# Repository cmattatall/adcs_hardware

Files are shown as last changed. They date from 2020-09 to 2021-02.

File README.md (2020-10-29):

# adcs_hardware
Hardware repository for ADCS

# Harware Architecture Overview

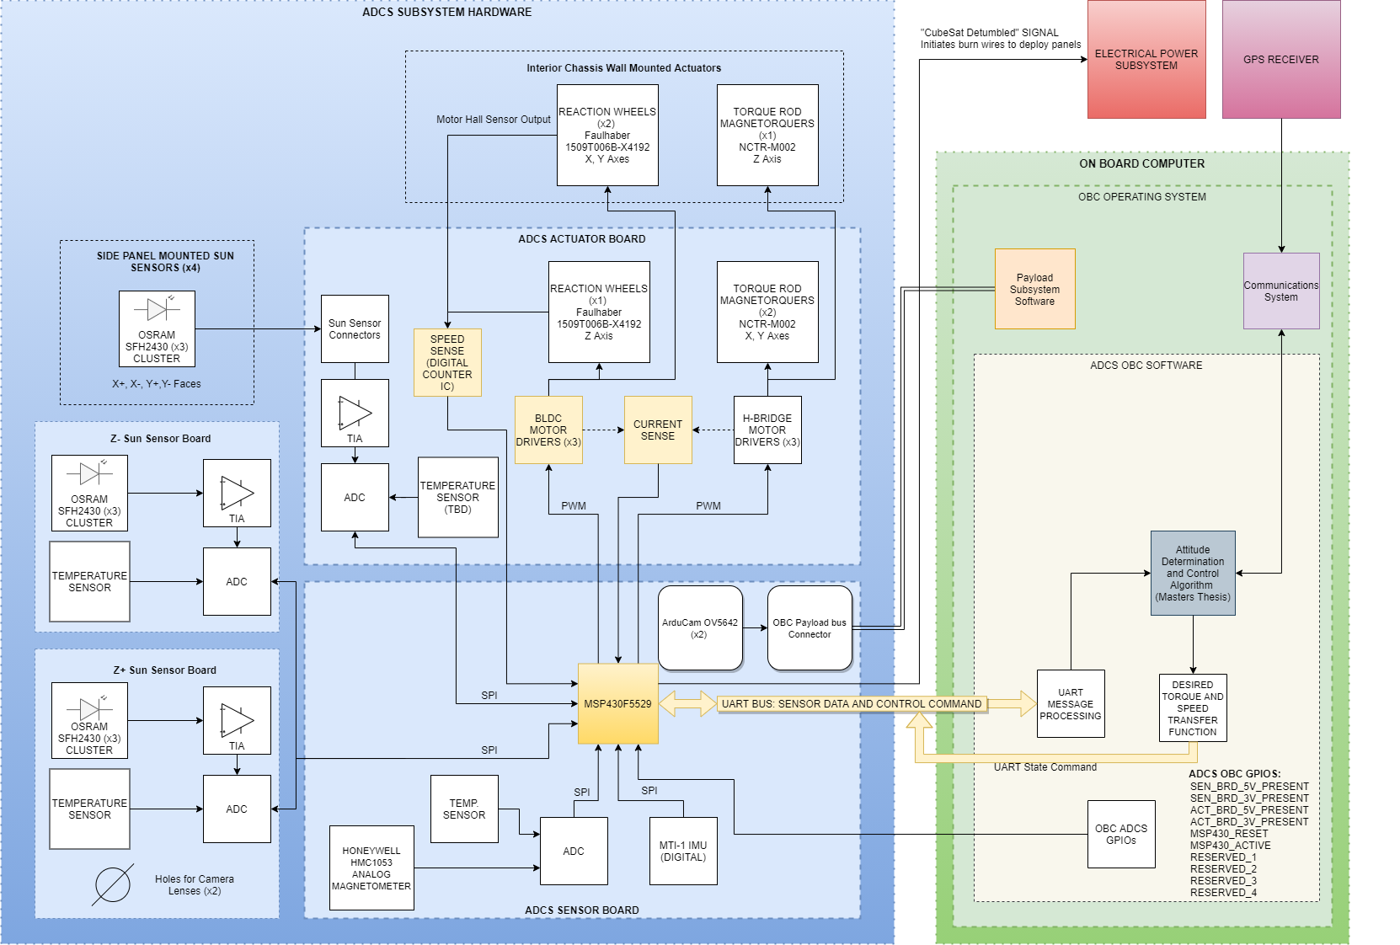
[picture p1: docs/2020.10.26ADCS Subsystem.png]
ADCS Hardware Block Diagram 2020.10.26


# VERSION CONTROL

WHENEVER A SHEMATIC REVISION IS COMPLETED, UNLIKE SOFTWARE, BRANCHES SHOULD NOT BE MERGED. THEY SHOULD BE FROZEN.

TO START A REVISION, THE CURRENT "HEAD" SHOULD BE FORKED (READ: MAKE A NEW BRANCH) NAMED APPROPRIATELY. 

If the revision is accepted and the design changes pass review, the revision branch then becomes the new master branch.

This way, the last "stable" revision branch (the old master branch) remains completely unchanged and unaffected by deltas made in the forked branch.

If there is ever an issue, the old version can be selected SIMPLY by switching back to the old branch, no merging should ever occur.

# Cloning repo for use in Eagle

Clone Repo into your local eagle projects repository
ie: C:/Users/user/Documents/Eagle/projects/

Repo will then appear under projects tab of the 'Control Panel' window when Eagle is launched.

# Eagle File Types Notes
 
## Project Manager File
*.epf is the eagle project manager file and contains all settings information for project. Contains all path references to all the libraries the have been used. *.epf is not crucial to project but can be useful to share with collaborators. 

## Design Files 
*.brd and *.sch files must have matching names and be contained in the same folder. Schematic files also copy all the information from the component libraries once the components are placed in a schematic, making the library files less necessary once used. The .brd files also copy the package information from the component libraries and don’t require libraries again unless you need to place a new component or replace a previous component. 

## Backup Files
*.b#x and *.s#x files are local backups by Eagle. By default Eagle saves 9 backups (9 is also the max).

## Libraries
Libraries are the templates for components. They are unique files that all the information on a specific component that Eagle CAD requires for design. They are the building blocks that contain information like pin numbers, terminal names, symbol shape, package type and footprint size etc. A library has both a symbol (used in schematics) and a package (footprint for pcb layout). Once a library is used in an Eagle design, it is no longer required as Eagle copies all the information over to the schematic and board files. However, while working with your team, it is recommended to share and use the same libraries to keep your designs consistent.

Custom library parts have been saved in managed library: https://library.io/libraries/22876504-my_library

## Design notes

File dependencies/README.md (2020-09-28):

# EDA DEPENDENCIES (EAGLE LIBS, DESIGN BLOCKS, CUSTOM FOOTPRINTS, AND OTHER DEPENDENCIES) GO HERE #

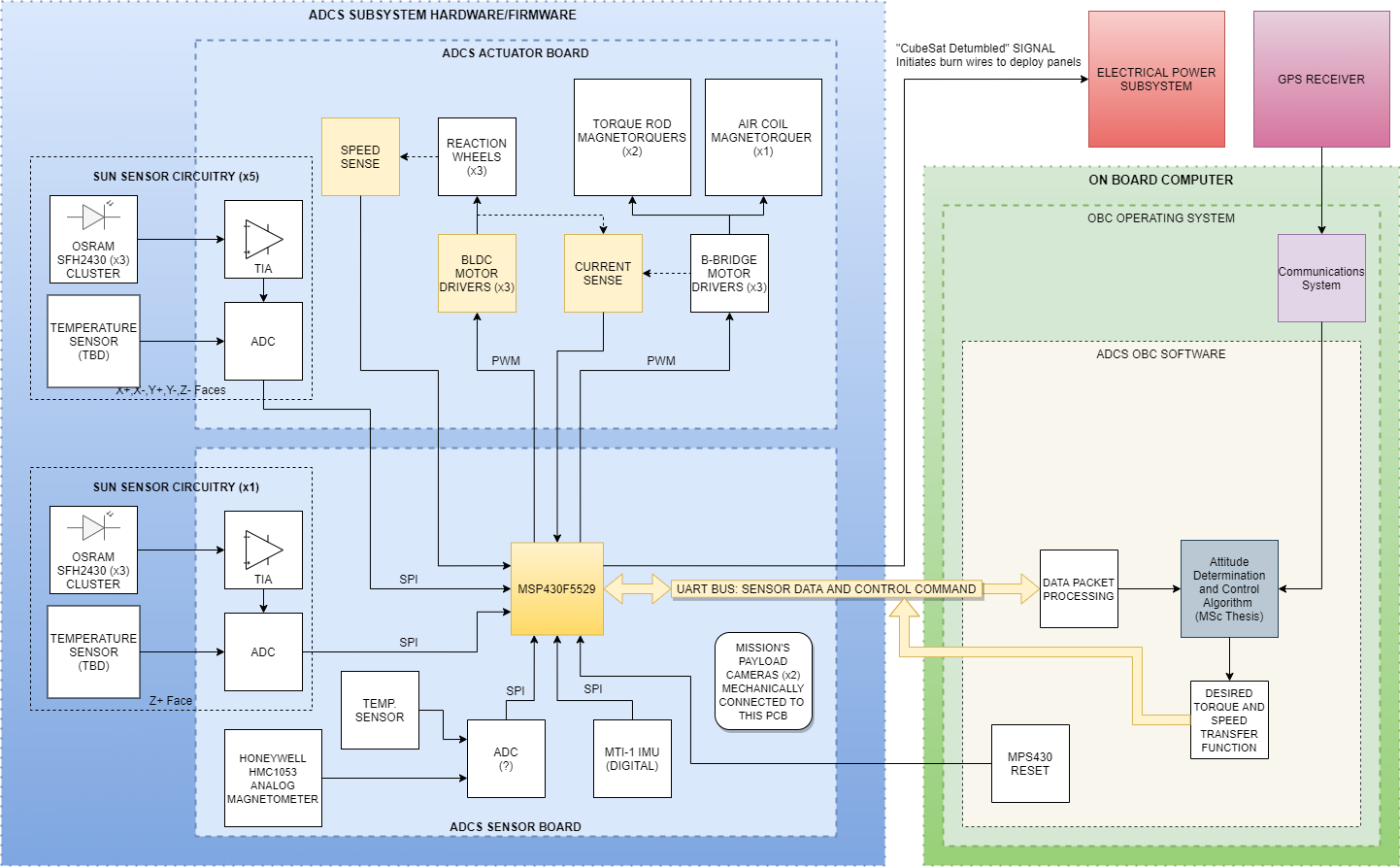
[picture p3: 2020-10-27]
docs/High Level Diagram 2020.09.08.png

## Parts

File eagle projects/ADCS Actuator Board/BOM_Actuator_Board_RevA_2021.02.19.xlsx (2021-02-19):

LORIS CubeSat Bill of Materials |  |  |  | Subsystem: ADCS
Dalhousie Space Systems Lab |  |  |  | PCB: Actuator Board | Rev: A |  | Date: 2021.02.19
Item | Qty | Manufacturer | MPN | Ref Des | Value | Footprint | Description | Digikey PN | Datasheet Link
1 | 12 | Yageo | AC0402KRX7R8BB223 | C54, C70, C71, C84, C98, C100, C101, C105, C110, C111, C115, C116 | 0.022u | C0402 | 0.022µF ±10% 25V Ceramic Capacitor X7R 0402 (1005 Metric) | 311-3068-1-ND | https://www.yageo.com/upload/media/product/productsearch/datasheet/mlcc/UPY-AC_NP0X7R_16V-to-630V_12.pdf
2 | 12 | Yageo | CC0603KRX7R8BB104 | C13, C16, C25, C26, C119, C121, C122, C126, C129, C130, C139, C142 | 0.1u | C0603 | 0.1µF ±10% 25V Ceramic Capacitor X7R 0603 (1608 Metric) | 311-1341-1-ND | https://www.yageo.com/upload/media/product/productsearch/datasheet/mlcc/UPY-GPHC_X7R_6.3V-to-50V_18.pdf
3 | 39 | Yageo | CS0402KRX7R8BB104 | C17, C21, C23, C27, C29, C37, C39, C43, C46, C48, C49, C51, C53, C56, C65, C67, C69, C73, C75, C76, C78, C79, C81, C83, C86, C88, C90, C92, C93, C95, C97, C102, C104, C107, C109, C112, C114, C123, C131 | 0.1u | C0402 | 0.1µF ±10% 25V Ceramic Capacitor X7R 0402 (1005 Metric) | 13-CS0402KRX7R8BB104CT-ND | https://www.yageo.com/upload/media/product/productsearch/datasheet/mlcc/UPY-ST_NPOX7R_16V-to-3KV_5.pdf
4 | 3 | Yageo | CC0603KRX7R8BB334 | C15, C125, C141 | 0.33u | C0603 | 0.33µF ±10% 25V Ceramic Capacitor X7R 0603 (1608 Metric) | 311-3573-1-ND | https://www.yageo.com/upload/media/product/productsearch/datasheet/mlcc/UPY-GPHC_X7R_6.3V-to-50V_18.pdf
5 | 3 | Yageo | CC0603KRX7R8BB474 | C64, C124, C132 | 0.47u | C0603 | 0.47µF ±10% 25V Ceramic Capacitor X7R 0603 (1608 Metric) | 311-1805-1-ND | https://www.yageo.com/upload/media/product/productsearch/datasheet/mlcc/UPY-GPHC_X7R_6.3V-to-50V_18.pdf
6 | 6 | TDK Corporation | CGA3E3X7R1H474M080AE | R19, R20, R48, R49, R83, R84 | 10K | R0603 | 0.47µF ±20% 50V Ceramic Capacitor X7R 0603 (1608 Metric) | 445-172476-1-ND | https://product.tdk.com/info/en/catalog/datasheets/mlcc_automotive_soft_en.pdf?ref_disty=digikey
7 | 9 | Yageo | RE0402FRE0710KL | R3, R4, R5, R6, R13, R14, R17, R30, R76 | 10k | R0402 | 10 kOhms ±1% 0.063W, 1/16W Chip Resistor 0402 (1005 Metric) Moisture Resistant Thick Film | 13-RE0402FRE0710KLCT-ND | https://www.yageo.com/upload/media/product/productsearch/datasheet/rchip/PYu-RE_105_RoHS_L_6.pdf
8 | 3 | Kemet | C0603C106M8PAC7411 | C42, C128, C144 | 10u | C0603 | 10µF ±20% 10V Ceramic Capacitor X5R 0603 (1608 Metric) | 399-C0603C106M8PAC7411CT-ND | https://api.kemet.com/component-edge/download/datasheet/C0603C106M8PAC7411.pdf
9 | 12 | Yageo | RC0402FR-0713K7L | R23, R28, R33, R39, R45, R51, R54, R57, R60, R63, R66, R69 | 13.7k | R0402 | 13.7 kOhms ±1% 0.063W, 1/16W Chip Resistor 0402 (1005 Metric) Moisture Resistant Thick Film | 311-13.7KLRCT-ND | https://www.yageo.com/upload/media/product/productsearch/datasheet/rchip/PYu-RC_Group_51_RoHS_L_11.pdf
10 | 3 | AVX Corporation | F981E105MMA | C14, C120, C140 | 1u | C0603 | 1µF Molded Tantalum Capacitors 25V 0603 (1608 Metric) 10Ohm | 478-8658-1-ND | http://datasheets.avx.com/F98.pdf
11 | 18 | Vishay Vitramon | VJ0402Y103KXJAC31 | C18, C22, C24, C28, C33, C40, C44, C45, C47, C50, C66, C72, C74, C77, C80, C89, C91, C94 | 1u | C0402 | 10000pF ±10% 16V Ceramic Capacitor X7R 0402 (1005 Metric) | 720-1250-1-ND | https://www.vishay.com/docs/45040/vj31vj34automlcc.pdf
12 | 3 | Kemet | C0603C225K4PACTU | C41, C127, C143 | 2.2u | C0603 | 2.2µF ±10% 16V Ceramic Capacitor X5R 0603 (1608 Metric) | 399-7886-1-ND | https://api.kemet.com/component-edge/download/datasheet/C0603C225K4PACTU.pdf
13 | 12 | Yageo | RC0402FR-07280RL | R22, R25, R32, R38, R44, R50, R53, R56, R59, R62, R65, R68 | 280R | R0402 | 280 Ohms ±1% 0.063W, 1/16W Chip Resistor 0402 (1005 Metric) Moisture Resistant Thick Film | 311-280LRCT-ND | https://www.yageo.com/upload/media/product/productsearch/datasheet/rchip/PYu-RC_Group_51_RoHS_L_11.pdf
14 | 6 | Yageo | RT0603FRE073K3L | R35, R36, R73, R74, R86, R87 | 3.3k | R0603 | 3.3 kOhms ±1% 0.1W, 1/10W Chip Resistor 0603 (1608 Metric) Thin Film | YAG3354CT-ND | https://www.yageo.com/upload/media/product/productsearch/datasheet/rchip/PYu-RT_1-to-0.01_RoHS_L_12.pdf
15 | 3 | Yageo | RC0402FR-0735KL | R18, R71, R77 | 35k | R0402 | 35 kOhms ±1% 0.063W, 1/16W Chip Resistor 0402 (1005 Metric) Moisture Resistant Thick Film | 13-RC0402FR-0735KLCT-ND | https://www.yageo.com/upload/media/product/productsearch/datasheet/rchip/PYu-RC_Group_51_RoHS_L_11.pdf
16 | 9 | Yageo | RC0402FR-074K7L | R1, R2, R7, R8, R9, R10, R11, R12, R15 | 4.7k | R0402 | 4.7 kOhms ±1% 0.063W, 1/16W Chip Resistor 0402 (1005 Metric) Moisture Resistant Thick Film | 311-4.7KLRCT-ND | https://www.yageo.com/upload/media/product/productsearch/datasheet/rchip/PYu-RC_Group_51_RoHS_L_11.pdf
17 | 12 | AVX Corporation | F981A475MMUAJ6 | C52, C55, C68, C82, C85, C87, C96, C99, C103, C106, C108, C113 | 4.7u | C0402 | 4.7µF Molded Tantalum Capacitors 10V 0603 (1608 Metric) 6Ohm @ 100kHz | 478-F981A475MMUAJ6CT-ND | http://datasheets.avx.com/F98.pdf
18 | 12 | Yageo | RC0402FR-073K74L | R24, R31, R34, R40, R46, R52, R55, R58, R61, R64, R67, R70 | 3.74k | R0402 | 3.74 kOhms ±1% 0.063W, 1/16W Chip Resistor 0402 (1005 Metric) Moisture Resistant Thick Film | 311-3.74KLRCT-ND | https://www.yageo.com/upload/media/product/productsearch/datasheet/rchip/PYu-RC_Group_51_RoHS_L_11.pdf
19 | 2 | Yageo | RC0603FR-07510RL | R26, R27 | 500R | R0603 | 510 Ohms ±1% 0.1W, 1/10W Chip Resistor 0603 (1608 Metric) Moisture Resistant Thick Film | 311-510HRCT-ND | https://www.yageo.com/upload/media/product/productsearch/datasheet/rchip/PYu-RC_Group_51_RoHS_L_11.pdf
20 | 3 | Yageo | RC0402FR-075R1L | R16, R29, R75 | 5R | R0402 | 5.1 Ohms ±1% 0.063W, 1/16W Chip Resistor 0402 (1005 Metric) Moisture Resistant Thick Film | YAG3370CT-ND | https://www.yageo.com/upload/media/product/productsearch/datasheet/rchip/PYu-RC_Group_51_RoHS_L_11.pdf
21 | 3 | Yageo | RT0603FRE0775KL | R21, R72, R85 | 75K | R0603 | 75 kOhms ±1% 0.1W, 1/10W Chip Resistor 0603 (1608 Metric) Thin Film | YAG5969CT-ND | https://www.yageo.com/upload/media/product/productsearch/datasheet/rchip/PYu-RT_1-to-0.01_RoHS_L_12.pdf
22 | 6 | Texas Instruments | ADS7841E/2K5 | U2, U3, U4, U13, U25, U27 | ADS7841E/2K5 |  | 12 Bit Analog to Digital Converter 4 Input 1 SAR 16-SSOP | 296-25900-1-ND | http://www.ti.com/lit/gpn/ADS7841
23 | 3 | Rohm Semiconductor | BD6210F-E2 | U9, U35, U39 | BD6210F-E2 | 8-SOP | Motor Driver Power MOSFET On/Off 8-SOP | BD6210F-E2CT-ND | http://rohmfs.rohm.com/en/products/databook/datasheet/ic/motor/dc/bd621x-e.pdf
24 | 15 | On Shore Technology Inc. | OSTVN02A150 | J7, J8, J9, J10, J11, J12, J13, J14, J15, J16, J17, J18, JX, JY, JZ | DNP | DO NOT POPULATE | TERM BLK 2P SIDE ENT 2.54MM PCB | ED10561-ND | http://www.on-shore.com/wp-content/uploads/OSTVNXXA150.pdf
25 | 3 | N/A | N/A | JP5, JP7, JP9 | DNP | DO NOT POPULATE | Pin Header Male 1x02 2.54MM | N/A | N/A
26 | 4 | N/A | N/A | J1, J4, J5, J6 | DNP | DO NOT POPULATE | Pin Header Male 1x03 2.54MM | N/A | N/A
27 | 2 | N/A | N/A | J2, J3 | DNP | DO NOT POPULATE | Pin Header Male 2x08 2.54MM | N/A | N/A
28 | 2 | N/A | N/A | MX, MY | DNP | DO NOT POPULATE | NCTR-M002 Torque Rod Assembly | N/A | N/A
29 | 1 | N/A | N/A | RWZ | DNP | DO NOT POPULATE | DSS LORIS Reaction Wheel Assembly | N/A | N/A
30 | 3 | Texas Instruments | DRV10970PWPR | U7, U10, U12 | DRV10970 | 24-HTSSOP | Motor Driver Power MOSFET PWM 24-HTSSOP | 296-44066-1-ND | http://www.ti.com/general/docs/suppproductinfo.tsp?distId=10
31 | 2 | Lite-On Inc. | LTST-C190GKT | LED1, LED2 | GREEN | LED0603 | Green 569nm LED Indication - Discrete 2.1V 0603 (1608 Metric) | 160-1183-1-ND | https://media.digikey.com/pdf/Data%20Sheets/Lite-On%20PDFs/LTST-C190GKT.pdf
32 | 3 | TE Connectivity AMP Connectors | 1-84953-1 | J19, J20, J21 | TE_1-84953-1 | SMD | 11 Position FPC Connector Contacts, Top 0.039" (1.00mm) Surface Mount, Right Angle | A101403CT-ND | https://www.te.com/commerce/DocumentDelivery/DDEController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
33 | 12 | Texas Instruments | TLV9051IDCKR | U6, U15, U19, U21, U23, U24, U26, U28, U29, U30, U31, U32 | TLV9051IDCKR | SC-70-5 | General Purpose Amplifier 1 Circuit Rail-to-Rail SC-70-5 | 296-TLV9051IDCKRCT-ND | http://www.ti.com/general/docs/suppproductinfo.tsp?distId=10
34 | 3 | STMicroelectronics | TSV991AILT | U1, U5, U8 | TSV991AILT | SOT-23-5 | General Purpose Amplifier 1 Circuit Rail-to-Rail SOT-23-5 | 497-5833-1-ND | http://www.st.com/content/ccc/resource/technical/document/datasheet/d8/e3/a5/aa/8f/d7/42/67/CD00144611.pdf/files/CD00144611.pdf/jcr:content/translations/en.CD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

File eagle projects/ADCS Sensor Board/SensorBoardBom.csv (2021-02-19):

Part | Value | Device | Package | Description
A1 | HMC1053PA0242 | HMC1053PA0242 | PA0242
A2 | ARDUCAM_OV5642 | ARDUCAM_OV5642 | ARDUCAM
A3 | ARDUCAM_OV5642 | ARDUCAM_OV5642 | ARDUCAM
C1 | 100n | C-EUC0402 | C0402 | CAPACITOR, European symbol
C2 | 10u | POLARIZED_CAP | A/3216-18R
C3 | 12p | C-EUC0402 | C0402 | CAPACITOR, European symbol
C4 | 12p | C-EUC0402 | C0402 | CAPACITOR, European symbol
C5 | 100n | C-EUC0402 | C0402 | CAPACITOR, European symbol
C6 | 470n | C-EUC0402 | C0402 | CAPACITOR, European symbol
C7 | 1n | C-EUC0402 | C0402 | CAPACITOR, European symbol
C8 | 100n | C-EUC0402 | C0402 | CAPACITOR, European symbol
C9 | 1u | C-EUC1206 | C1206 | CAPACITOR, European symbol
C10 | 0.1u | C-EUC0603 | C0603 | CAPACITOR, European symbol
C11 | 0.1u | C-EUC0603 | C0603 | CAPACITOR, European symbol
C12 | 1u | C-EUC1206 | C1206 | CAPACITOR, European symbol
C13 | 1u | C-EUC1206 | C1206 | CAPACITOR, European symbol
C14 | 0.1u | C-EUC0603 | C0603 | CAPACITOR, European symbol
C15 | 0.1u | C-EUC0603 | C0603 | CAPACITOR, European symbol
C16 | 0.1u | C-EUC0603 | C0603 | CAPACITOR, European symbol
C17 | 1n | C-EUC0805 | C0805 | CAPACITOR, European symbol
C18 | 1n | C-EUC1206 | C1206 | CAPACITOR, European symbol
C19 | 0.1u | C-EUC0603 | C0603 | CAPACITOR, European symbol
C20 | 0.1u | C-EUC0603 | C0603 | CAPACITOR, European symbol
C21 | 1n | C-EUC0805 | C0805 | CAPACITOR, European symbol
C22 | 0.1u | C-EUC0603 | C0603 | CAPACITOR, European symbol
C23 | 1n | C-EUC0805 | C0805 | CAPACITOR, European symbol
C24 | 470n | C-EUC0805 | C0805 | CAPACITOR, European symbol
J1 | HDR_10_EZFET_DEBUGGER | HDR_10_EZFET_DEBUGGER | HDRV10W66P254_10X1_2540X254H858
J2 | MTI-1_8428-11B1-RK-TP | MTI-1_8428-11B1-RK-TP | PLCC-28_SOCKET_TH
JP1 |  | PINHD-1X4 | 1X04 | PIN HEADER
JP2 |  | PINHD-2X8 | 2X08 | PIN HEADER
JP3 |  | PINHD-2X8 | 2X08 | PIN HEADER
JP4 |  | PINHD-1X4 | 1X04 | PIN HEADER
JP5 |  | PINHD-2X6 | 2X06 | PIN HEADER
JP6 |  | JP1Q_ | 1X02 | JUMPER
JP7 |  | PINHD-1X7 | 1X07 | PIN HEADER
JP8 |  | PINHD-1X4 | 1X04 | PIN HEADER
JP9 |  | PINHD-1X3 | 1X03 | PIN HEADER
LED1 |  | LEDCHIP-LED0603 | CHIP-LED0603 | LED
LED2 |  | LEDCHIP-LED0603 | CHIP-LED0603 | LED
LED3 |  | LEDCHIP-LED0603 | CHIP-LED0603 | LED
MH1 | MTGP700H400 | MTGP700H400 | MTGP700H400
MH2 | MTGP700H400 | MTGP700H400 | MTGP700H400
MH3 | MTGP700H400 | MTGP700H400 | MTGP700H400
MH4 | MTGP700H400 | MTGP700H400 | MTGP700H400
Q1 | BC850SMD | BC850SMD | SOT23-BEC | NPN Transistor
Q2 | IRF7507TRPBF | IRF7507TRPBF | SOP8P65_300X490X111L53X30N
R1 | 0R | R-US_R0402 | R0402 | RESISTOR, American symbol
R2 | 1k | R-US_R0402 | R0402 | RESISTOR, American symbol
R3 | 2k | R-US_R0402 | R0402 | RESISTOR, American symbol
R4 | 1k | R-US_R0402 | R0402 | RESISTOR, American symbol
R5 | 2k | R-US_R0402 | R0402 | RESISTOR, American symbol
R6 | 1M | R-US_R0402 | R0402 | RESISTOR, American symbol
R7 | 47k | R-US_R0402 | R0402 | RESISTOR, American symbol
R8 | 470R | R-US_R0603 | R0603 | RESISTOR, American symbol
R9 | 200R | R-US_R1206 | R1206 | RESISTOR, American symbol
R10 | 1k | R-US_R0805 | R0805 | RESISTOR, American symbol
R11 | 1k | R-US_R0805 | R0805 | RESISTOR, American symbol
R12 | 5.6k | R-US_R0805 | R0805 | RESISTOR, American symbol
R13 | 5.6k | R-US_R0805 | R0805 | RESISTOR, American symbol
R14 | 1.37M | R-US_R0805 | R0805 | RESISTOR, American symbol
R15 | 1.37M | R-US_R0805 | R0805 | RESISTOR, American symbol
R16 | 0R | R-US_R0805 | R0805 | RESISTOR, American symbol
R17 | 1k | R-US_R0805 | R0805 | RESISTOR, American symbol
R18 | 1k | R-US_R0805 | R0805 | RESISTOR, American symbol
R19 | 5.1M | R-US_R1206 | R1206 | RESISTOR, American symbol
R20 | 5.6k | R-US_R0805 | R0805 | RESISTOR, American symbol
R21 | 5.6k | R-US_R0805 | R0805 | RESISTOR, American symbol
R22 | 1.37M | R-US_R0805 | R0805 | RESISTOR, American symbol
R23 | 1.37M | R-US_R0805 | R0805 | RESISTOR, American symbol
R24 | 1k | R-US_R0805 | R0805 | RESISTOR, American symbol
R25 | 1k | R-US_R0805 | R0805 | RESISTOR, American symbol
R26 | 5.6k | R-US_R0805 | R0805 | RESISTOR, American symbol
R27 | 5.6k | R-US_R0805 | R0805 | RESISTOR, American symbol
R28 | 1.37M | R-US_R0805 | R0805 | RESISTOR, American symbol
R29 | 1.37M | R-US_R0805 | R0805 | RESISTOR, American symbol
R30 | 27R | R-US_R0805 | R0805 | RESISTOR, American symbol
R31 | 470R | R-US_R0603 | R0603 | RESISTOR, American symbol
R32 | 750R | R-US_R0603 | R0603 | RESISTOR, American symbol
R33 | 0R | R-US_R0805 | R0805 | RESISTOR, American symbol
R34 | 0R | R-US_R0805 | R0805 | RESISTOR, American symbol
R35 | 0R | R-US_R0805 | R0805 | RESISTOR, American symbol
S1 | RST | 10-XX | B3F-10XX | OMRON SWITCH
TP1 | TESTPOINT | TESTPOINT | TP_P76H50
TP2 | TESTPOINT | TESTPOINT | TP_P76H50
TP3 | TESTPOINT | TESTPOINT | TP_P76H50
TP4 | TESTPOINT | TESTPOINT | TP_P76H50
TP5 | TESTPOINT | TESTPOINT | TP_P76H50
U1 | MSP430F5529IPN | MSP430F5529IPN | QFP80P50_1400X1400X160L60X22N
U2 | LMV321 | LMV321 | SOT23-5P65_210X110L36X22N
U3 | ADS7841E_2K5 | ADS7841E_2K5 | DBQ16
U4 | LMV321 | LMV321 | SOT23-5P65_210X110L36X22N
U5 | LMV321 | LMV321 | SOT23-5P65_210X110L36X22N
Y1 | 32.768kHz | MS3V-T1R | MS3V-T1R
Y2 | CSTCR4M00G15L99 | CSTCR4M00G15L996M00G53Z | MURATA-FILTER_CSTCR

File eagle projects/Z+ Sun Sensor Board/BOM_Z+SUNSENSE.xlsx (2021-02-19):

LORIS ADCS |  |  |  | BILL OF MATERIALS
BOARD: Z+ SUN SENSE BOARD |  |  |  | REV A | Date: 2021.02.14
Item | Qty | MPN | Reference Designator | Value | Footprint | Description | Datasheet
1 | 1 | DO NOT POPULATE | A1 | DO NOT POPULATE | Custom | Sun Sensor Mount | -
2 | 3 | VJ0402Y103KXJAC31 | C14, C16, C21 | 1u | C0402 | CAP CER 10000PF 16V X7R 0402 | https://www.vishay.com/docs/45040/vj31vj34automlcc.pdf
3 | 8 | CS0402KRX7R8BB104 | C12, C15, C19, C20, C22, C26, C29, C31 | 0.1u | C0402 | CAP CER 0.1UF 25V X7R 0402 | https://www.yageo.com/upload/media/product/productsearch/datasheet/mlcc/UPY-ST_NPOX7R_16V-to-3KV_5.pdf
4 | 3 | CL21B475KOFNNNE | C25, C28, C30 | 4.7u | C0805 | CAP CER 4.7UF 16V X7R 0805 | https://media.digikey.com/pdf/Data%20Sheets/Samsung%20PDFs/CL_Series_MLCC_ds.pdf
5 | 3 | AC0402KRX7R8BB223 | C27, C32, C33 | 0.022u | C0402 | CAP CER 0.022UF 25V X7R 0402 | https://www.yageo.com/upload/media/product/productsearch/datasheet/mlcc/UPY-AC_NP0X7R_16V-to-630V_12.pdf
6 | 3 | DO NOT POPULATE | J4, J5, J6 | DO NOT POPULATE | DO NOT POPULATE | Terminal Block Connector 1x02 | -
7 | 1 | DO NOT POPULATE | JP3 | DO NOT POPULATE | DO NOT POPULATE | PIN HEADER | -
8 | 3 | RC0402FR-07280RL | R1, R8, R14 | 280R | R0402 | RES SMD 280 OHM 1% 1/16W 0402 | https://www.yageo.com/upload/media/product/productsearch/datasheet/rchip/PYu-RC_Group_51_RoHS_L_11.pdf
9 | 1 | RC0805JR-070RL | R2 | 0R | R0805 | RES SMD 0 OHM JUMPER 1/8W 0805 | https://www.yageo.com/upload/media/product/productsearch/datasheet/rchip/PYu-RC_Group_51_RoHS_L_11.pdf
10 | 1 | RE0402FRE0710KL | R20 | 10k | R0402 | RES SMD 10K OHM 1% 1/16W 0402 | https://www.yageo.com/upload/media/product/productsearch/datasheet/rchip/PYu-RE_105_RoHS_L_6.pdf
11 | 1 | RC0402JR-075M1L | R26 | 5.1M | R0402 | RES SMD 5.1M OHM 5% 1/16W 0402 | https://www.yageo.com/upload/media/product/productsearch/datasheet/rchip/PYu-RC_Group_51_RoHS_L_11.pdf
12 | 3 | RC0402FR-0713K7L | R3, R9, R15 | 13.7k | R0402 | RES SMD 13.7K OHM 1% 1/16W 0402 | https://www.yageo.com/upload/media/product/productsearch/datasheet/rchip/PYu-RC_Group_51_RoHS_L_11.pdf
13 | 3 | RC0402FR-073K74L | R7, R13, R19 | 5.6k | R0402 | RES SMD 3.74K OHM 1% 1/16W 0402 | https://www.yageo.com/upload/media/product/productsearch/datasheet/rchip/PYu-RC_Group_51_RoHS_L_11.pdf
14 | 1 | ADS7841E | U2 | ADS7841E_2K5 | DBQ16 | 12 Bit Analog to Digital Converter 4 Input 1 SAR 16-SSOP | http://www.ti.com/lit/gpn/ADS7841
15 | 1 | LM20BIM7X | U4 | LM20BIM7X_NOPB | SOT23-5P65_210X110L40X22N_LM20 | Temperature Sensor Analog, Local -55°C ~ 130°C 11.77mV/°C SC-70-5 | https://www.ti.com/lit/ds/symlink/lm20.pdf?ts=1611799060094
16 | 3 | TLV9051IDCKR | U6, U8, U9 | TLV9051IDCKR | SC70-5P65_210X110L36X22N_TLV9051 | General Purpose Amplifier 1 Circuit Rail-to-Rail SC-70-5 | https://www.ti.com/lit/ds/symlink/tlv9051.pdf?HQS=dis-dk-null-digikeymode-dsf-pf-null-wwe&ts=1611796011779

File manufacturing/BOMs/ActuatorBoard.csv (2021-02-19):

Item | QTY | MPN | REFDES | Value | Footprint | Description | Source | Link
1 | 3 | RE0402FRE0710KL | R37, R43, R49 | 10K | 402 | Metal film resistor | Digikey | https://www.digikey.ca/en/products/detail/yageo/RE0402FRE0710KL/5922980
2 | 3 | RC0402FR-0735KL | R36, R42, R48 | 35K | 402 | Metal film resistor | Digikey | https://www.digikey.ca/en/products/detail/yageo/RC0402FR-0735KL/5917655
3 | 38 | CC0603JPX7R9BB104 | C2, C7, C9, C10, C12, C13, C14, C15, C16, C17, C18, C19, C21, C22, C23, C24, C25, C26, C27, C28, C31, C35, C40, C44, C46, C51, C53, C54, C57, C59, C68, C73, C75, C76, C90, C95, C97, C98 | 100n | 603 | X7R Ceramic Capacitor | Digikey | https://www.digikey.ca/en/products/detail/yageo/CC0603JPX7R9BB104/11490924
4 | 3 | C1608X7R1H334M080AC | C30, C34, C38 | 330n | 603 | X7R Ceramic Capacitor | Digikey | https://www.digikey.ca/en/products/detail/tdk-corporation/C1608X7R1H334M080AC/2443429
5 | 3 | CGA3E3X7R1H474M080AE | C39, C41, C42, C61 | 470n | 603 | X7R Ceramic Capacitor | Digikey | https://www.digikey.ca/en/products/detail/tdk-corporation/CGA3E3X7R1H474M080AE/4989851
6 | 42 | CGA3E3X7R1H474M080AE | R1,R2, R3, R4, R5, R6, R7, R8, R9, R10, R11, R12, R29, R30, R31, R32, R33, R38, R44, R60, R61, R85, R86, R87, R88, R89, R92, R93, R100, R101, R102, R103, R104, R105, R106, R107, R108, R109, R110, R111, R125, R126, | 10K | 603 | Metal film resistor | Digikey | https://www.digikey.ca/en/products/detail/yageo/RT0603FRD0710KL/5928954
7 | 3 |  | C29, C33, C37 | 10u | 603
8 | 24 | RC0603FR-0713K7L | R14, R15, R16, R17, R18, R19, R114, R115, R116, R117, R118, R119, R164, R165, R166, R167, R168, R169, R214, R215, R216, R217, R218, R219 | 13.7K | 603 | Metal film resistor | Digikey | https://www.digikey.ca/en/products/detail/yageo/RC0603FR-0713K7L/726933
9 | 19 | UMK107AB7105KA-T | C6, C8, C11, C20, C32, C36, C43, C50, C52, C55, C56, C58, C60, C72, C74, C77, C94, C96, C99 | 1u | 603 | X7R Ceramic Capacitor | Digikey | https://www.digikey.ca/en/products/detail/taiyo-yuden/UMK107AB7105KA-T/3660085
10 | 6 | RT0603FRE073K3L | R124, R127, R129, R130, R132, R133 | 3.3K | 603 | Metal film resistor | Digikey | https://www.digikey.ca/en/products/detail/yageo/RT0603FRE073K3L/1075348
11 | 4 |  | C1, C45, C67, C89 | 4.7u | 603
12 | 19 | RC0603FR-075M1L | R20, R21, R24, R25, R34, R39, R40, R45, R46, R53, R54, R55, R59, R120, R121, R170, R171, R220, R221 | 5.1M | 603 | Metal film resistor | Digikey | https://www.digikey.ca/en/products/detail/yageo/RC0603FR-075M1L/5918378
13 | 3 | RC0402FR-075R1L | R35, R41, R47 | 5R | 402 | Metal film resistor | Digikey | https://www.digikey.ca/en/products/detail/yageo/RC0402FR-075R1L/5917722
14 | 3 | RT0603FRE0775KL | R112, R128, R131 | 75K | 603 | Metal film resistor | Digikey | https://www.digikey.ca/en/products/detail/yageo/RT0603FRE0775KL/1075486
15 | 6 | ADS7841E/2K5 | U1, U9, U12, U13, U19, U25 | N/A | DBQ16 | 12Bit ADC : SPI Interface | Digikey | https://www.digikey.com/en/products/detail/texas-instruments/ADS7841E-2K5/300663
16 | 3 | BD6210F-E2 | U4, U5, U6 | N/A | SOP8 | H-bridge IC | Digikey | https://www.digikey.ca/en/products/detail/rohm-semiconductor/BD6210F-E2/1936313
17 | 19 | BSS138 | Q2, Q3, Q4, Q5, Q6, Q7, Q8, Q9, Q10, Q11, Q12, Q13, Q14, Q15, Q16, Q17, Q18, Q19, Q21 | N/A | SOT233 | N channel Discrete enhancement mode MOSFET | Digikey | https://www.digikey.com/en/products/detail/on-semiconductor/BSS138/244210
18 | 1 | CD4514BM96 | U14 | N/A | 24-SOIC | 4-bit latched line decoder | Digikey | https://www.digikey.ca/en/products/detail/texas-instruments/CD4514BM96/1691558
19 | 3 | DRV10970PWPR | U17, U18, U20 | N/A | 24-HTSSOP | 3-phase brushless DC motor driver IC | Digikey | https://www.digikey.ca/en/products/detail/texas-instruments/DRV10970PWPR/5985442
23 | 1 | REF194GSZ-REEL7 | U2 | N/A | 8-SOIC | Series voltage reference IC | Digikey | https://www.digikey.ca/en/products/detail/analog-devices-inc/REF194GSZ-REEL7/995868
24 | 12 | SFH 2430-Z | D4, D5, D6, D13, D14, D15, D19, D20, D21, D25, D26, D27 | N/A | 2-SMD, Gull Wing | Optoisolator | Digikey | https://www.digikey.ca/en/products/detail/osram-opto-semiconductors-inc/SFH-2430-Z/1668853
25 | 3 | SN74HC165DB | U8, U11, U16 | N/A | SOP16 | 8 bit parallel shift register | AliExpress | https://www.aliexpress.com/item/4000854321406.html
26 | 3 | SN74HC590AD | U7, U10, U14 | N/A | 16-SOIC | 8 bit binary counter | Digikey | https://www.digikey.com/en/products/detail/texas-instruments/SN74HC590AD/376756
27 | 4 | TLV9054IDR | U3, U15, U21, U27 | N/A | 14-SOIC | single rail CMOS OP-AMP | Digikey | https://www.digikey.com/en/products/detail/texas-instruments/TLV9054IDR/10273198
28 | 3 | TSV991AILT | U7, U8, U10 | N/A | SOT-23-5 | dual rail CMOS OP-AMP 20Mhz | Mouser | https://www.mouser.com/ProductDetail/STMicroelectronics/TSV991AILT/?qs=NCG0bTVqH4ejiP6AM1B8jw==
29 | 3 | Do not populate | JP1, JP2, JP3 | N/A | Do not populate | 0.1’ pitch male 1x2 rectangular pin header | Do not populate | Do not populate
30 | 1 | Do not populate | JP5 | N/A | Do not populate | Solder jumper | Do not populate | Do not populate
31 | 12 | Do not populate | TP1, TP2, TP3, TP4, TP5, TP6, TP7, TP8, TP9, TP10, TP11, TP12 | N/A | Do not populate | 0.1’ pitch male 1x1 rectangular pin header | Do not populate | Do not populate
32 | 3 | Do not populate | MX, MY, MZ | NCTR-M002_MOUNT | Do not populate | MQTR MOUNTING FRAME | Do not populate | Do not populate
33 | 3 | Do not populate | A1, A2, A3 | REACTION_WHEELASSEMBLY | Do not populate | RW MOUNTING FRAME | Do not populate | Do not populate

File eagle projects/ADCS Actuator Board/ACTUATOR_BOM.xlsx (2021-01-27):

LORIS ADCS ACTUATOR BOARD BILL OF MATERIALS (REVISION A)
Item | Qty | MPN | Reference Designator | Value | Footprint | Description | Source | Link
1 | 3 | RC0402FR-075R1L | R35, R41, R47 | 5R | 402 | Thick film resistor | Digikey | https://www.digikey.ca/en/products/detail/yageo/RC0402FR-075R1L/5917722
2 | 12 | RC0402FR-07280RL | R22, R25, R32, R38, R44, R50, R53, R56, R59, R62, R65, R68 | 280R | 402 | Thick film resistor | Digikey | https://www.digikey.ca/en/products/detail/yageo/RC0402FR-07280RL/726578
3 | 12 | RT0402BRD073K74L | R24, R31, R34, R40, R46, R52, R55, R58, R61, R64, R67, R70 | 3.74K | 402 | Thick film resistor | Digikey | https://www.digikey.ca/en/products/detail/yageo/RT0402BRD073K74L/1069258
4 | 9 | RE0402FRE0710KL | R13, R3, R4, R5, R6, R7, R36, R42, R48 | 10K | 402 | Thick film resistor | Digikey | https://www.digikey.ca/en/products/detail/yageo/RE0402FRE0710KL/5922980
5 | 12 | RC0402FR-0713K7L | R23, R28, R33, R39, R45, R51, R54, R57, R60, R63, R66, R69 | 13.7K | 402 | Thick film resistor | Digikey | https://www.digikey.ca/en/products/detail/yageo/RC0402FR-0713K7L/2827638
6 | 3 | RC0402FR-0735KL | R37, R43, R49 | 35K | 402 | Thick film resistor | Digikey | https://www.digikey.ca/en/products/detail/yageo/RC0402FR-0735KL/5917655
7 | 2 | RC0603FR-07510RL | R26, R27 | 500R | 603 | Thick film resistor | Digikey | https://www.digikey.ca/en/products/detail/yageo/RC0603FR-07510RL/727285
8 | 6 | RT0603FRE073K3L | R124, R127, R129, R130, R132, R133 | 3.3K | 603 | Thick film resistor | Digikey | https://www.digikey.ca/en/products/detail/yageo/RT0603FRE073K3L/1075348
9 | 7 | CGA3E3X7R1H474M080AE | R2, R8, R9, R10, R11, R100, R101 | 10K | 603 | Thick film resistor | Digikey | https://www.digikey.ca/en/products/detail/yageo/RT0603FRD0710KL/5928954
10 | 1 | RC0603FR-0724KL | R1 | 24K | 603 | Thick film resistor | Digikey | https://www.digikey.ca/en/products/detail/yageo/RC0603FR-0724KL/727076
11 | 3 | RT0603FRE0775KL | R112, R128, R131 | 75K | 603 | Thick film resistor | Digikey | https://www.digikey.ca/en/products/detail/yageo/RT0603FRE0775KL/1075486
12 | 12 | AC0402KRX7R8BB223 | C54, C70, C71, C84, C98, C100, C101, C105, C110, C111, C115, C116 | 0.022u | 402 | Ceramic SMD MLCC Capacitor | Digikey | https://www.digikey.ca/en/products/detail/yageo/AC0402KRX7R8BB223/6643054
13 | 28 | CS0402KRX7R8BB104 | C46, C48, C49, C51, C53, C65, C67, C69, C73, C75, C76, C78, C79, C81, C83, C86, C88, C90, C92, C93, C95, C97, C102, C104, C107, C109, C112, C114 | 0.1u | 402 | Ceramic SMD MLCC Capacitor | Digikey | https://www.digikey.ca/en/products/detail/yageo/CS0402KRX7R8BB104/6097896
14 | 12 | VJ0402Y103KXJAC31 | C28, C45, C47, C50, C66, C72, C74, C77, C80, C89, C91, C94 | 1u | 402 | Ceramic SMD MLCC Capacitor | Digikey | https://www.digikey.ca/en/products/detail/vishay-vitramon/VJ0402Y103KXJAC31/2972205
15 | 18 | F981A475MMUAJ6 | C2, C3, C4, C5, C6, C7, C52, C55, C68, C82, C85, C87, C96, C99, C103, C106, C108, C113 | 4.7u | 402 | SMD Molded Tantalum Capacitor | Digikey | https://www.digikey.ca/en/products/detail/avx-corporation/F981A475MMUAJ6/12321753
16 | 21 | CC0603KRX7R8BB104 | C1, C12, C13, C14, C15, C16, C17, C18, C19, C21, C23, C31, C35, C40, C44, C57, C59, C61, C62, C63, C64 | 0.1u | 603 | Ceramic SMD MLCC Capacitor | Digikey | https://www.digikey.ca/en/products/detail/yageo/CC0603KRX7R8BB104/2103079
17 | 3 | CC0603KRX7R8BB334 | C30, C34, C38 | 0.33u | 603 | Ceramic SMD MLCC Capacitor | Digikey | https://www.digikey.ca/en/products/detail/yageo/CC0603KRX7R8BB334/5883785
18 | 3 | CC0603KRX7R8BB474 | C39, C41, C42 | 0.47u | 603 | Ceramic SMD MLCC Capacitor | Digikey | https://www.digikey.ca/en/products/detail/yageo/CC0603KRX7R8BB474/5195213
19 | 7 | F981E105MMA | C20, C32, C36, C43, C56, C58, C60 | 1u | 603 | SMD Molded Tantalum Capacitor | Digikey | https://www.digikey.ca/en/products/detail/avx-corporation/F981E105MMA/4005086
20 | 1 | PLEASE QUOTE | LED1 | RED | 603 | Mono color Chip LED | FABRICATOR PROVIDED
21 | 1 | PLEASE QUOTE | LED2 | ORANGE | 603 | Mono color Chip LED | FABRICATOR PROVIDED
22 | 6 | ADS7841E/2K5 | U4, U9, U12, U13, U25, U27 | N/A | DBQ16 | 12Bit ADC : SPI Interface | Digikey | https://www.digikey.com/en/products/detail/texas-instruments/ADS7841E-2K5/300663
23 | 3 | BD6210F-E2 | U11, U16, U22 | N/A | SOP8 | H-bridge IC | Digikey | https://www.digikey.ca/en/products/detail/rohm-semiconductor/BD6210F-E2/1936313
24 | 3 | DRV10970PWPR | U17, U18, U20 | N/A | 24-HTSSOP | 3-phase brushless DC motor driver IC | Digikey | https://www.digikey.ca/en/products/detail/texas-instruments/DRV10970PWPR/5985442
25 | 12 | SFH 2430-Z | D1, D3, D5, D7, D8, D9, D10, D11, D12, D13, D14, D15 | N/A | 2-SMD, Gull Wing | Optoisolator | Digikey | https://www.digikey.ca/en/products/detail/osram-opto-semiconductors-inc/SFH-2430-Z/1668853
26 | 12 | TLV9051IDCKR | U6, U15, U19, U21, U23, U24, U26, U28, U29, U30, U31, U32 | N/A | 14-SOIC | single rail CMOS OP-AMP | Digikey | https://www.digikey.ca/en/products/detail/texas-instruments/TLV9051IDCKR/10715332
27 | 3 | TSV991AILT | U7, U8, U10 | N/A | SOT-23-5 | dual rail CMOS OP-AMP 20Mhz | Mouser | https://www.mouser.com/ProductDetail/STMicroelectronics/TSV991AILT/?qs=NCG0bTVqH4ejiP6AM1B8jw==
28 | 3 | DO NOT POPULATE | JP1, JP2, JP3 | DO NOT POPULATE |  | DO NOT POPULATE
29 | 1 | DO NOT POPULATE | J1 | DO NOT POPULATE |  | DO NOT POPULATE
30 | 2 | DO NOT POPULATE | J2, J3 | DO NOT POPULATE |  | DO NOT POPULATE
31 | 3 | DO NOT POPULATE | JX, JY, JZ | DO NOT POPULATE |  | DO NOT POPULATE
32 | 3 | DO NOT POPULATE | J4, J5, J6 | DO NOT POPULATE |  | DO NOT POPULATE

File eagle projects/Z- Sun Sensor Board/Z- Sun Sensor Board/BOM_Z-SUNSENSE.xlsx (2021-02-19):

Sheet: ZMinusSunSensorBoard
LORIS ADCS |  |  |  | BILL OF MATERIALS
BOARD: Z- SUN SENSE BOARD |  |  |  | REVISION: A | Date: 2021.01.28
Item | Qty | MPN | Reference Designator | Value | Footprint | Description | Package | Datasheet
1 | 1 | DO NOT POPULATE | A1 | DO NOT POPULATE | Custom | Sun Sensor Mount | SUN_SENOR_MASK | -
2 | 3 | VJ0402Y103KXJAC31 | C14, C16, C21 | 1u | 0402 | CAP CER 10000PF 16V X7R 0402 | C0402 | https://www.vishay.com/docs/45040/vj31vj34automlcc.pdf
3 | 8 | CS0402KRX7R8BB104 | C12, C15, C19, C20, C22, C26, C29, C31 | 0.1u | 0402 | CAP CER 0.1UF 25V X7R 0402 | C0402 | https://www.yageo.com/upload/media/product/productsearch/datasheet/mlcc/UPY-ST_NPOX7R_16V-to-3KV_5.pdf
4 | 3 | CL21B475KOFNNNE | C25, C28, C30 | 4.7u | 0805 | CAP CER 4.7UF 16V X7R 0805 | C0805 | https://media.digikey.com/pdf/Data%20Sheets/Samsung%20PDFs/CL_Series_MLCC_ds.pdf
5 | 3 | AC0402KRX7R8BB223 | C27, C32, C33 | 0.022u | 0402 | CAP CER 0.022UF 25V X7R 0402 | C0402 | https://www.yageo.com/upload/media/product/productsearch/datasheet/mlcc/UPY-AC_NP0X7R_16V-to-630V_12.pdf
6 | 3 | DO NOT POPULATE | J4, J5, J6 | DO NOT POPULATE | DO NOT POPULATE | Terminal Block Connector 1x02 | 2POL254 | -
7 | 1 | DO NOT POPULATE | JP3 | DO NOT POPULATE | DO NOT POPULATE | PIN HEADER | 1X06 | -
8 | 3 | RC0402FR-07280RL | R1, R8, R14 | 280R | 0402 | RES SMD 280 OHM 1% 1/16W 0402 | R0402 | https://www.yageo.com/upload/media/product/productsearch/datasheet/rchip/PYu-RC_Group_51_RoHS_L_11.pdf
9 | 1 | RC0805JR-070RL | R2 | 0R | 0805 | RES SMD 0 OHM JUMPER 1/8W 0805 | R0805 | https://www.yageo.com/upload/media/product/productsearch/datasheet/rchip/PYu-RC_Group_51_RoHS_L_11.pdf
10 | 1 | RE0402FRE0710KL | R20 | 10k | 0402 | RES SMD 10K OHM 1% 1/16W 0402 | R0402 | https://www.yageo.com/upload/media/product/productsearch/datasheet/rchip/PYu-RE_105_RoHS_L_6.pdf
11 | 1 | RC0402JR-075M1L | R26 | 5.1M | 0402 | RES SMD 5.1M OHM 5% 1/16W 0402 | R0603 | https://www.yageo.com/upload/media/product/productsearch/datasheet/rchip/PYu-RC_Group_51_RoHS_L_11.pdf
12 | 3 | RC0402FR-0713K7L | R3, R9, R15 | 13.7k | 0402 | RES SMD 13.7K OHM 1% 1/16W 0402 | R0402 | https://www.yageo.com/upload/media/product/productsearch/datasheet/rchip/PYu-RC_Group_51_RoHS_L_11.pdf
13 | 3 | RC0402FR-073K74L | R7, R13, R19 | 3.74k | 0402 | RES SMD 3.74K OHM 1% 1/16W 0402 | R0402 | https://www.yageo.com/upload/media/product/productsearch/datasheet/rchip/PYu-RC_Group_51_RoHS_L_11.pdf
14 | 1 | ADS7841E | U2 | ADS7841E_2K5 | 16-SSOP | 12 Bit Analog to Digital Converter 4 Input 1 SAR 16-SSOP | DBQ16 | http://www.ti.com/lit/gpn/ADS7841
15 | 1 | LM20BIM7X | U4 | LM20BIM7X_NOPB | SC-70-5 | Temperature Sensor Analog, Local -55°C ~ 130°C 11.77mV/°C SC-70-5 | SOT23-5P65_210X110L40X22N_LM20 | https://www.ti.com/lit/ds/symlink/lm20.pdf?ts=1611799060094
16 | 3 | TLV9051IDCKR | U6, U8, U9 | TLV9051IDCKR | SC-70-5 | General Purpose Amplifier 1 Circuit Rail-to-Rail SC-70-5 | SC70-5P65_210X110L36X22N_TLV9051 | https://www.ti.com/lit/ds/symlink/tlv9051.pdf?HQS=dis-dk-null-digikeymode-dsf-pf-null-wwe&ts=1611796011779

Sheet: BOM_ZMinusSunSensorBoard
LORIS ADCS Z- SUN SENSOR BOARD BILL OF MATERIALS (REVISION A)

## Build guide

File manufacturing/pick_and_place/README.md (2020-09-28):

# PICK AND PLACE FILES GO IN THIS FOLDER #

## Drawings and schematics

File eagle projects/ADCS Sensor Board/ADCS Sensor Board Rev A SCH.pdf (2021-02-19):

## Analog VCC

A

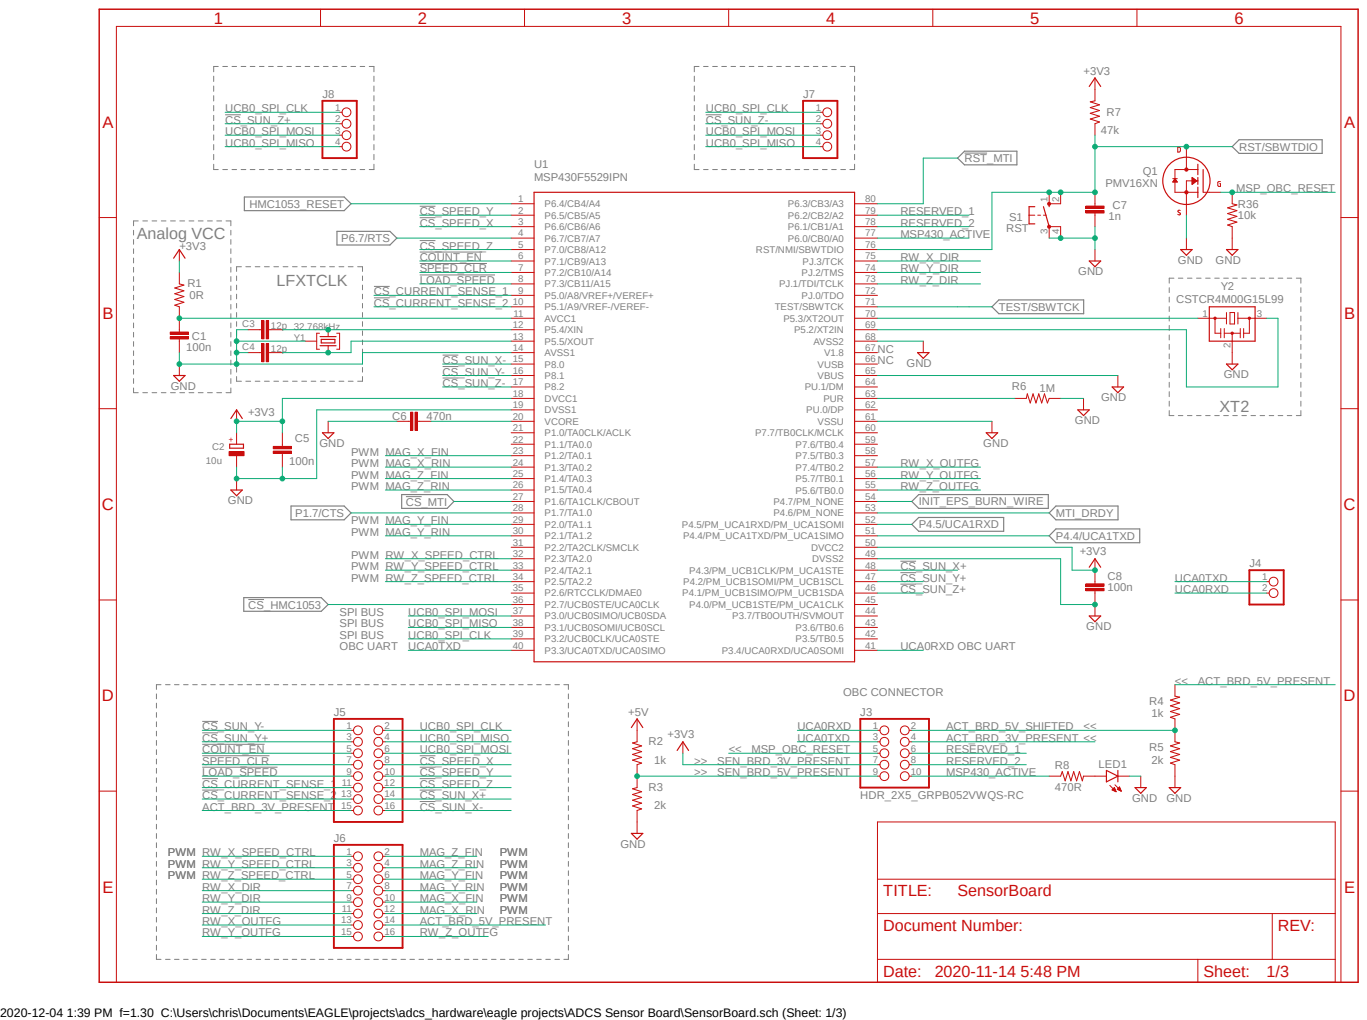
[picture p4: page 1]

C3 | 12p 32.768kHz | P5.4/XIN 12

Y1 | | | P5.5/XOUT 13

Document Number: | REV:

Date: 2020-11-14 5:48 PM | Sheet: 1/3

2020-12-04 1:39 PM f=1.30 C:\Users\chris\Documents\EAGLE\projects\adcs_hardware\eagle projects\ADCS Sensor Board\SensorBoard.sch (Sheet: 1/3)

A

A

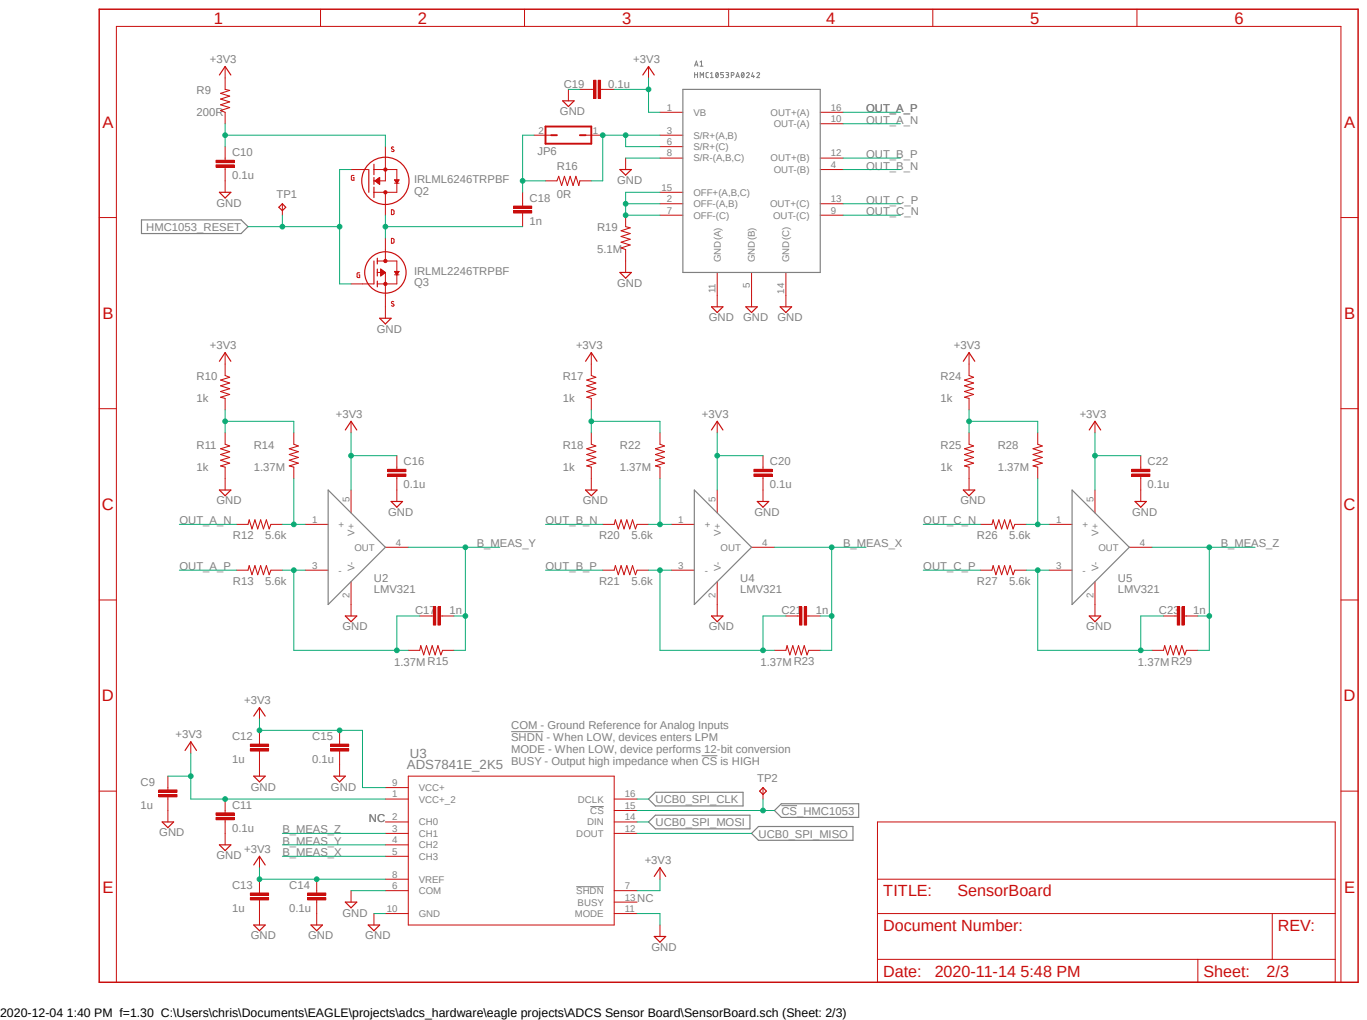
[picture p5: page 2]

COM - Ground Reference for Analog Inputs
SHDN - When LOW, devices enters LPM
MODE - When LOW, device performs 12-bit conversion
BUSY - Output high impedance when CS is HIGH

Document Number: | REV:

2020-12-04 1:40 PM f=1.30 C:\Users\chris\Documents\EAGLE\projects\adcs_hardware\eagle projects\ADCS Sensor Board\SensorBoard.sch (Sheet: 2/3)

A

A

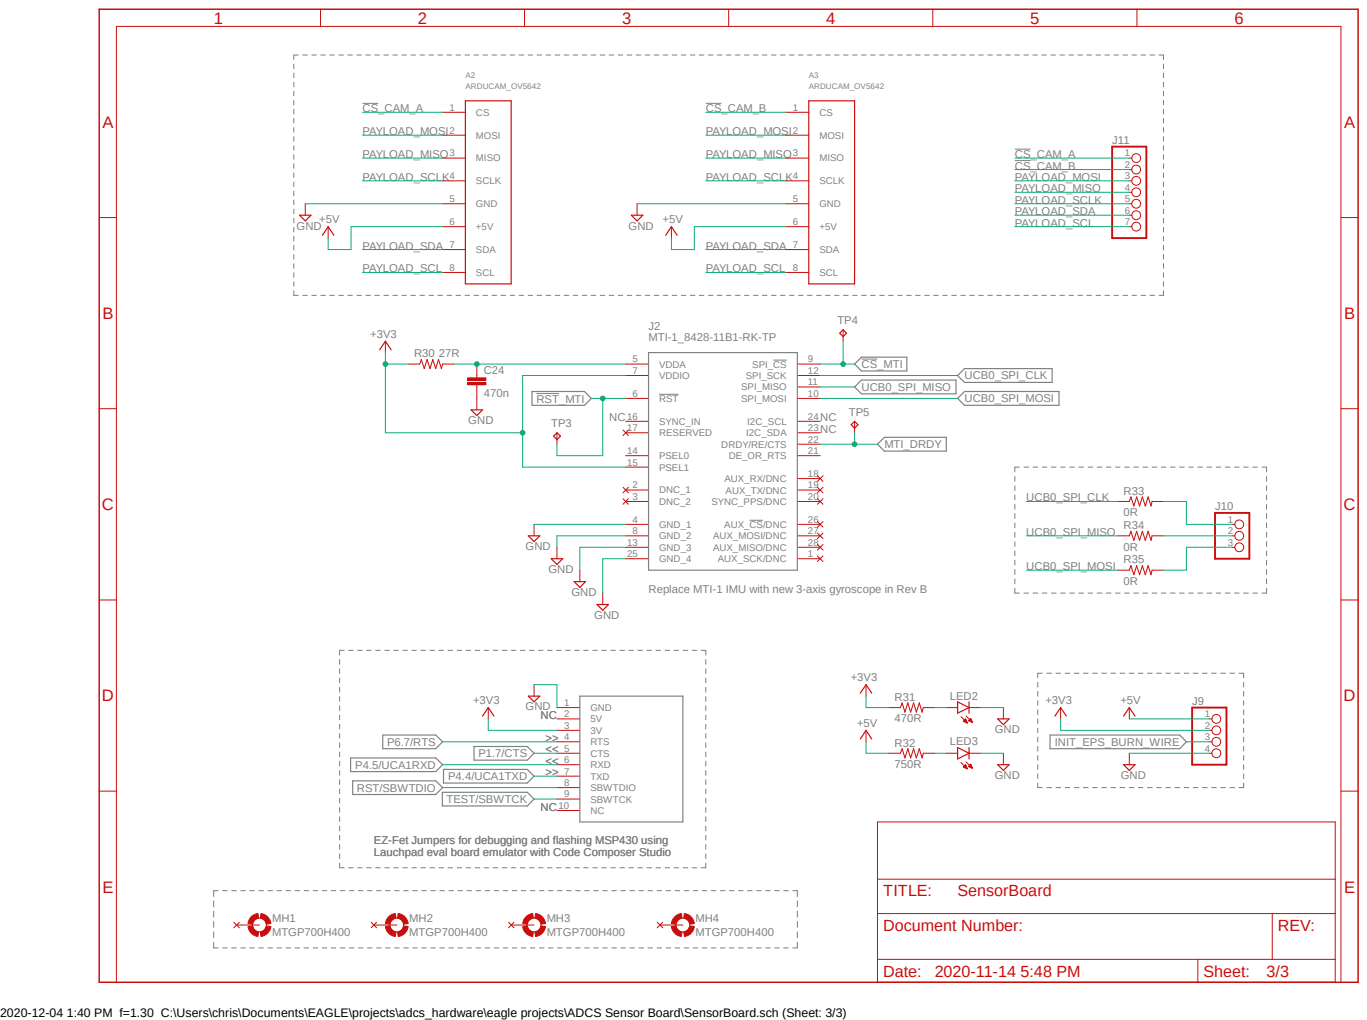
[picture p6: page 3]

VDDIO 7

RST 6 SYNC_IN 16 RESERVED 17 PSEL1 15 PSEL0 14

Replace MTI-1 IMU with new 3-axis gyroscope in Rev B

EZ-Fet Jumpers for debugging and flashing MSP430 using
Lauchpad eval board emulator with Code Composer Studio

Document Number: | REV:

2020-12-04 1:40 PM f=1.30 C:\Users\chris\Documents\EAGLE\projects\adcs_hardware\eagle projects\ADCS Sensor Board\SensorBoard.sch (Sheet: 3/3)

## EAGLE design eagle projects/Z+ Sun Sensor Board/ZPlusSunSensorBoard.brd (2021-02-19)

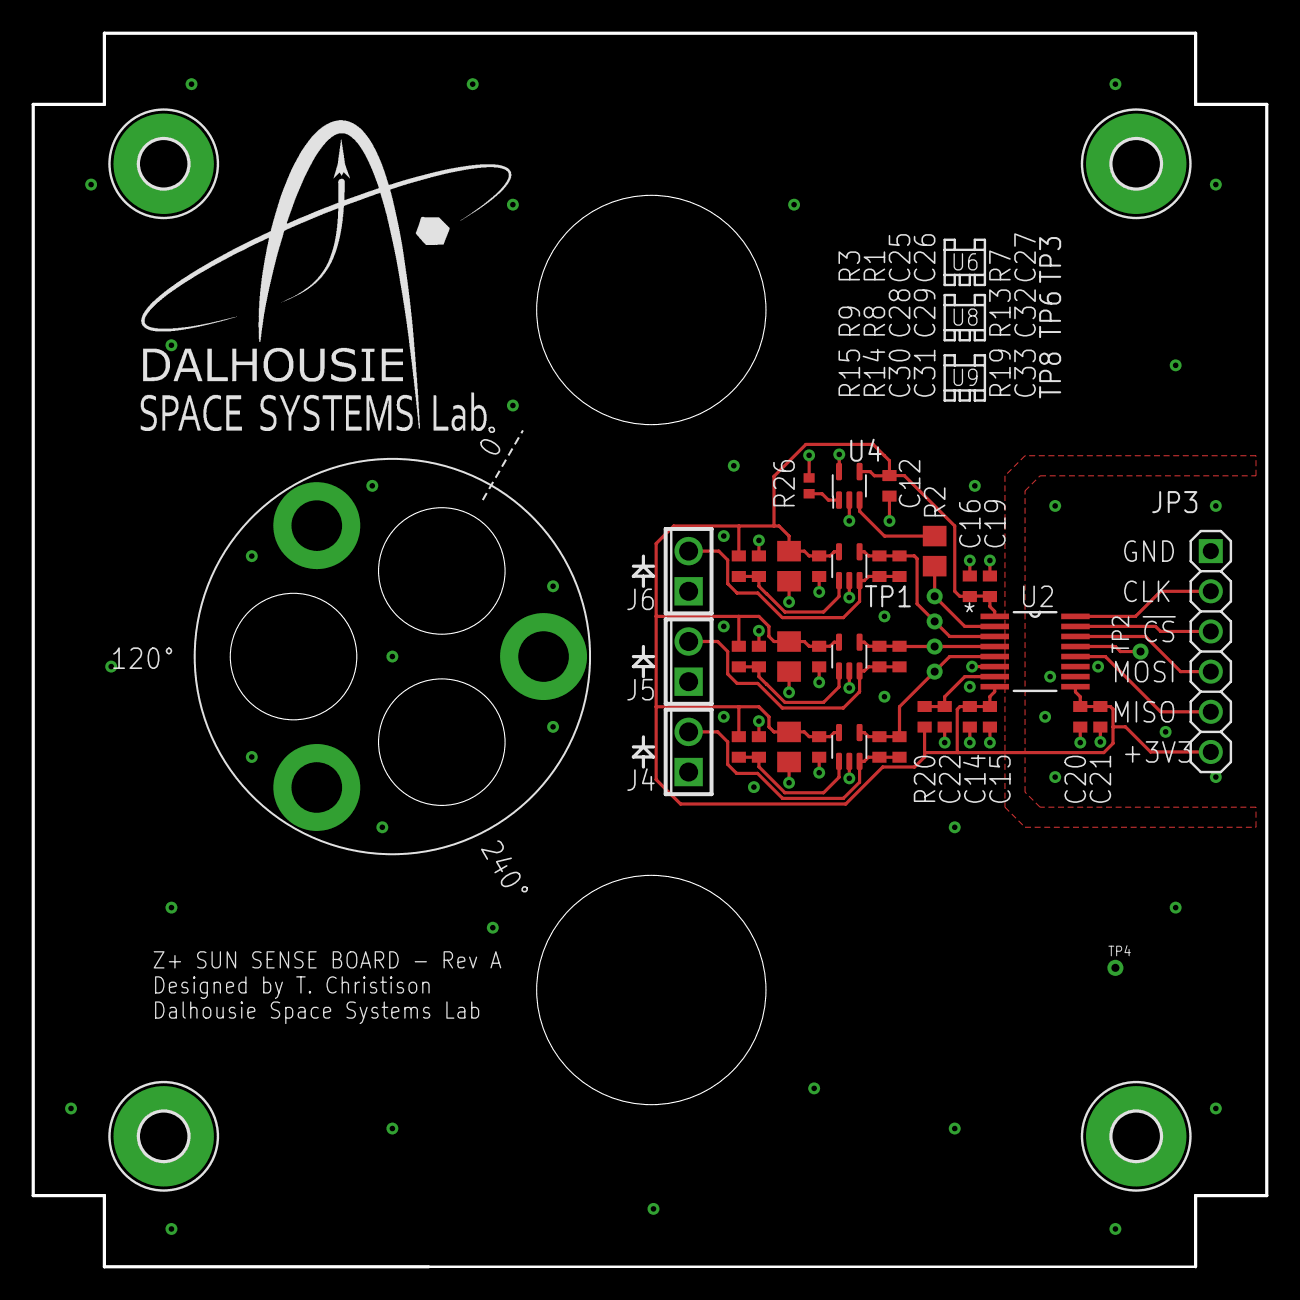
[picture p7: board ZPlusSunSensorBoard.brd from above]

Board: 2 copper layers, 78.0 x 78.0 mm, 50 parts (0 on the bottom side), 20 nets.

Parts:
A1: SUN_SENSOR_MOUNT; SUN_SENOR_MASK
C12, C15, C19, C20, C22, C26, C29, C31: 0.1u; C0402
C14, C16, C21: 1u; C0402
C25, C28, C30: 4.7u; C0805
C27, C32, C33: 0.022u; C0402
DRILEGEND: DRILEGEND
H1, H2, H3, H4: MOUNT-PAD-ROUND; PC104
J4, J5, J6: 2POL254
JP3: 1X06
R1, R8, R14: 280R; R0402
R2: 0R; R0805
R3, R9, R15: 13.7k; R0402
R7, R13, R19: 3.74k; R0402
R20: 10k; R0402
R26: 5.1M; R0402
TP1, TP2, TP3, TP4, TP6, TP8: TESTPOINT; TP_P76H50
U2: ADS7841E_2K5; DBQ16
U4: LM20BIM7X_NOPB; SOT23-5P65_210X110L40X22N_LM20
U6, U8, U9: TLV9051IDCKR; SC70-5P65_210X110L36X22N_TLV9051

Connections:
0_DEGREES: C27.2, R7.2, TP3.1, U2.3, U6.4
120_DEGREES: C32.2, R13.2, TP6.1, U2.4, U8.4
240_DEGREES: C33.2, R19.2, TP8.1, U2.5, U9.4
!CS!_SUN_Z+: JP3.3, U2.15
+3V3: C12.1, C14.1, C15.1, C16.1, C19.1, C20.1, C21.1, C25.1, C26.1, C28.1, C29.1, C30.1, C31.1, JP3.6, R3.2, R9.2, R15.2, R20.2, U2.1, U2.8, U2.9, U4.4, U6.5, U8.5, U9.5
GND: C12.2, C14.2, C15.2, C16.2, C19.2, C20.2, C21.2, C22.2, C25.2, C26.2, C28.2, C29.2, C30.2, C31.2, J4.1, J5.1, J6.1, JP3.1, R1.1, R8.1, R14.1, R26.2, TP4.1, U2.6, U2.10, U2.11, U4.2, U4.5, U6.2, U8.2, U9.2
unnamed: R2.1, U4.3
unnamed: TP2.1, U2.13
unnamed: C27.1, J6.2, R7.1, U6.3
unnamed: R1.2, R3.1, U6.1
unnamed: R26.1, U4.1
unnamed: C32.1, J5.2, R13.1, U8.3
unnamed: R8.2, R9.1, U8.1
unnamed: C33.1, J4.2, R19.1, U9.3
unnamed: R14.2, R15.1, U9.1
unnamed: C22.1, R20.1, U2.7
TEMP: R2.2, TP1.1, U2.2
UCB0_SPI_CLK: JP3.2, U2.16
UCB0_SPI_MISO: JP3.5, U2.12
UCB0_SPI_MOSI: JP3.4, U2.14

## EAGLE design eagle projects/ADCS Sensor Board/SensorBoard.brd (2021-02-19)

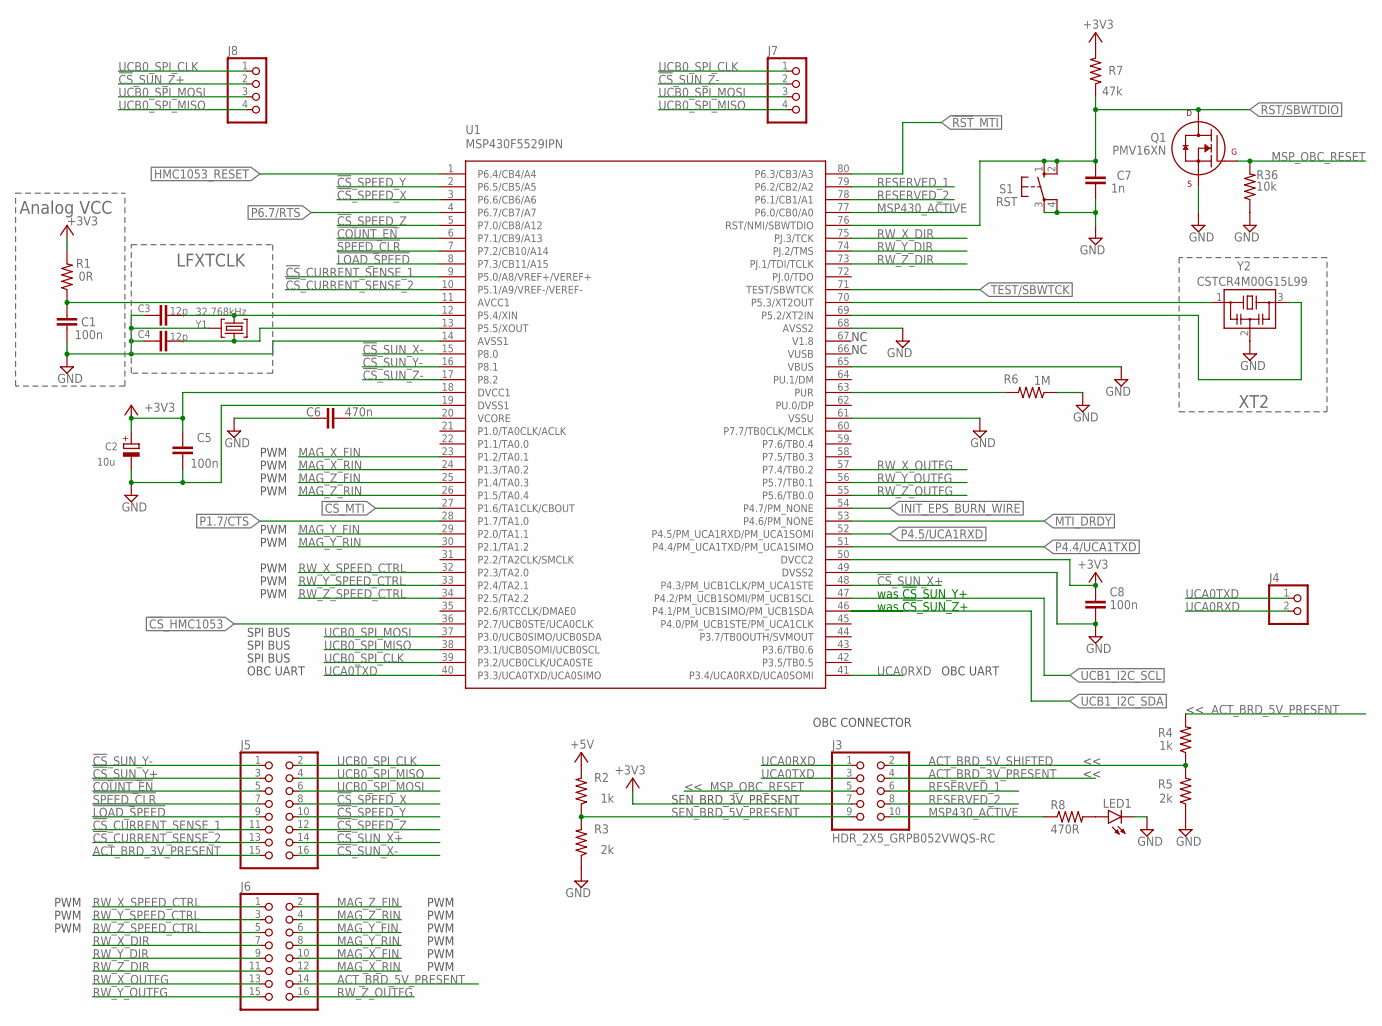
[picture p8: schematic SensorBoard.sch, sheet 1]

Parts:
C1, C5, C8: 100n; C0402
C2: 10u; A/3216-18R
C3, C4: 12p; C0402
C6: 470n; C0402
C7: 1n; C0402
J3: HDR_2X5_GRPB052VWQS-RC; GRPB052VWQS-RC
J4: HDR_1X2_; 1X02
J5, J6: PINHD-2X8; 2X08
J7, J8: PINHD-1X4; 1X04
LED1: LEDCHIP-LED0603; CHIP-LED0603
Q1: PMV16XN; SOT23-3P95_230X110L20X43N_PMV16XN
R1: 0R; R0402
R2, R4: 1k; R0603
R3, R5: 2k; R0603
R6: 1M; R0603
R7: 47k; R0402
R8: 470R; R0603
R36: 10k; R0603
S1: RST; B3F-10XX
U1: MSP430F5529IPN; QFP80P50_1400X1400X160L60X22N
Y1: 32.768kHz; MS3V-T1R
Y2: CSTCR4M00G15L99; MURATA-FILTER_CSTCR

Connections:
!COUNT_EN: J5.5, U1.6 (P7.1/CB9/A13)
!CS!_CURRENT_SENSE_1: J5.11, U1.9 (P5.0/A8/VREF+/VEREF+)
!CS!_CURRENT_SENSE_2: J5.13, U1.10 (P5.1/A9/VREF-/VEREF-)
!CS!_HMC1053: U1.36 (P2.7/UCB0STE/UCA0CLK); also elsewhere on the board
!CS!_MTI: U1.27 (P1.6/TA1CLK/CBOUT)
!CS!_SPEED_X: J5.8, U1.3 (P6.6/CB6/A6)
!CS!_SPEED_Y: J5.10, U1.2 (P6.5/CB5/A5)
!CS!_SPEED_Z: J5.12, U1.5 (P7.0/CB8/A12)
!CS!_SUN_X+: J5.16, U1.48 (P4.3/PM_UCB1CLK/PM_UCA1STE)
!CS!_SUN_X-: J5.14, U1.15 (P8.0)
!CS!_SUN_Y+: J5.3
!CS!_SUN_Y-: J5.1, U1.16 (P8.1)
!CS!_SUN_Z+: J8.2
!CS!_SUN_Z-: J7.2, U1.17 (P8.2)
!LOAD_SPEED: J5.9, U1.8 (P7.3/CB11/A15)
!RST!_MTI: U1.80 (P6.3/CB3/A3)
!SPEED_CLR: J5.7, U1.7 (P7.2/CB10/A14)
+3V3: C2.+, C5.2, C8.1, J3.7, R1.2, R7.2, U1.18 (DVCC1), U1.50 (DVCC2); also elsewhere on the board
+5V: R2.2; also elsewhere on the board
ACT_BRD_3V_PRESENT: J3.4, J5.15
ACT_BRD_5V_PRESENT: J6.14, R4.2
ACT_BRD_5V_SHIFTED: J3.2, R4.1, R5.2
AVCC1: C1.1, R1.1, U1.11 (AVCC1)
GND: C1.2, C2.-, C3.1, C4.1, C5.1, C6.1, C7.2, C8.2, LED1.C, Q1.2 (S), R3.1, R5.1, R6.1, R36.1, S1.3, S1.4 (P1), U1.14 (AVSS1), U1.19 (DVSS1), U1.49 (DVSS2), U1.61 (VSSU), U1.65 (VBUS), U1.68 (AVSS2), Y1.P3 (GND), Y2.2; also elsewhere on the board
HMC1053_RESET: U1.1 (P6.4/CB4/A4); also elsewhere on the board
INIT_EPS_BURN_WIRE: U1.54 (P4.7/PM_NONE); also elsewhere on the board
MAG_X_FIN: J6.10, U1.23 (P1.2/TA0.1)
MAG_X_RIN: J6.12, U1.24 (P1.3/TA0.2)
MAG_Y_FIN: J6.6, U1.29 (P2.0/TA1.1)
MAG_Y_RIN: J6.8, U1.30 (P2.1/TA1.2)
MAG_Z_FIN: J6.2, U1.25 (P1.4/TA0.3)
MAG_Z_RIN: J6.4, U1.26 (P1.5/TA0.4)
MSP430_ACTIVE: J3.10, R8.1, U1.77 (P6.0/CB0/A0)
MSP_OBC_RESET: J3.5, Q1.1 (G), R36.2
MTI_DRDY: U1.53 (P4.6/PM_NONE)
unnamed: LED1.A, R8.2
P1.7/CTS: U1.28 (P1.7/TA1.0); also elsewhere on the board
P4.4/UCA1TXD: U1.51 (P4.4/PM_UCA1TXD/PM_UCA1SIMO); also elsewhere on the board
P4.5/UCA1RXD: U1.52 (P4.5/PM_UCA1RXD/PM_UCA1SOMI); also elsewhere on the board
P5.2/XT2IN1: U1.69 (P5.2/XT2IN), Y2.3
P5.3/XT2OUT1: U1.70 (P5.3/XT2OUT), Y2.1
P5.4/XIN1: C3.2, U1.12 (P5.4/XIN), Y1.P2 (2)
P5.5/XOUT1: C4.2, U1.13 (P5.5/XOUT), Y1.P1 (1)
P6.7/RTS: U1.4 (P6.7/CB7/A7); also elsewhere on the board
RESERVED_1: J3.6, U1.79 (P6.2/CB2/A2)
RESERVED_2: J3.8, U1.78 (P6.1/CB1/A1)
RST/SBWTDIO: C7.1, Q1.3 (D), R7.1, S1.1 (S), S1.2 (S1), U1.76 (RST/NMI/SBWTDIO); also elsewhere on the board
RW_X_DIR: J6.7, U1.75 (PJ.3/TCK)
RW_X_OUTFG: J6.13, U1.57 (P7.4/TB0.2)
RW_X_SPEED_CTRL: J6.1, U1.32 (P2.3/TA2.0)
RW_Y_DIR: J6.9, U1.74 (PJ.2/TMS)
RW_Y_OUTFG: J6.15, U1.56 (P5.7/TB0.1)
RW_Y_SPEED_CTRL: J6.3, U1.33 (P2.4/TA2.1)
RW_Z_DIR: J6.11, U1.73 (PJ.1/TDI/TCLK)
RW_Z_OUTFG: J6.16, U1.55 (P5.6/TB0.0)
RW_Z_SPEED_CTRL: J6.5, U1.34 (P2.5/TA2.2)
SEN_BRD_5V_PRESENT: J3.9, R2.1, R3.2
TARGET_PUR: R6.2, U1.63 (PUR)
TEST/SBWTCK: U1.71 (TEST/SBWTCK); also elsewhere on the board
UCA0RXD: J3.1, J4.2, U1.41 (P3.4/UCA0RXD/UCA0SOMI)
UCA0TXD: J3.3, J4.1, U1.40 (P3.3/UCA0TXD/UCA0SIMO)
UCB0_SPI_CLK: J5.2, J7.1, J8.1, U1.39 (P3.2/UCB0CLK/UCA0STE); also elsewhere on the board
UCB0_SPI_MISO: J5.4, J7.4, J8.4, U1.38 (P3.1/UCB0SOMI/UCB0SCL); also elsewhere on the board
UCB0_SPI_MOSI: J5.6, J7.3, J8.3, U1.37 (P3.0/UCB0SIMO/UCB0SDA); also elsewhere on the board
UCB1_I2C_SCL: U1.47 (P4.2/PM_UCB1SOMI/PM_UCB1SCL); also elsewhere on the board
UCB1_I2C_SDA: U1.46 (P4.1/PM_UCB1SIMO/PM_UCB1SDA); also elsewhere on the board
VCORE1: C6.2, U1.20 (VCORE)

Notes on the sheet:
LFXTCLK
XT2
Analog VCC
OBC CONNECTOR
PWM
OBC UART
SPI BUS
SEN_BRD_3V_PRESENT
was !CS!_SUN_Y+
was !CS!_SUN_Z+

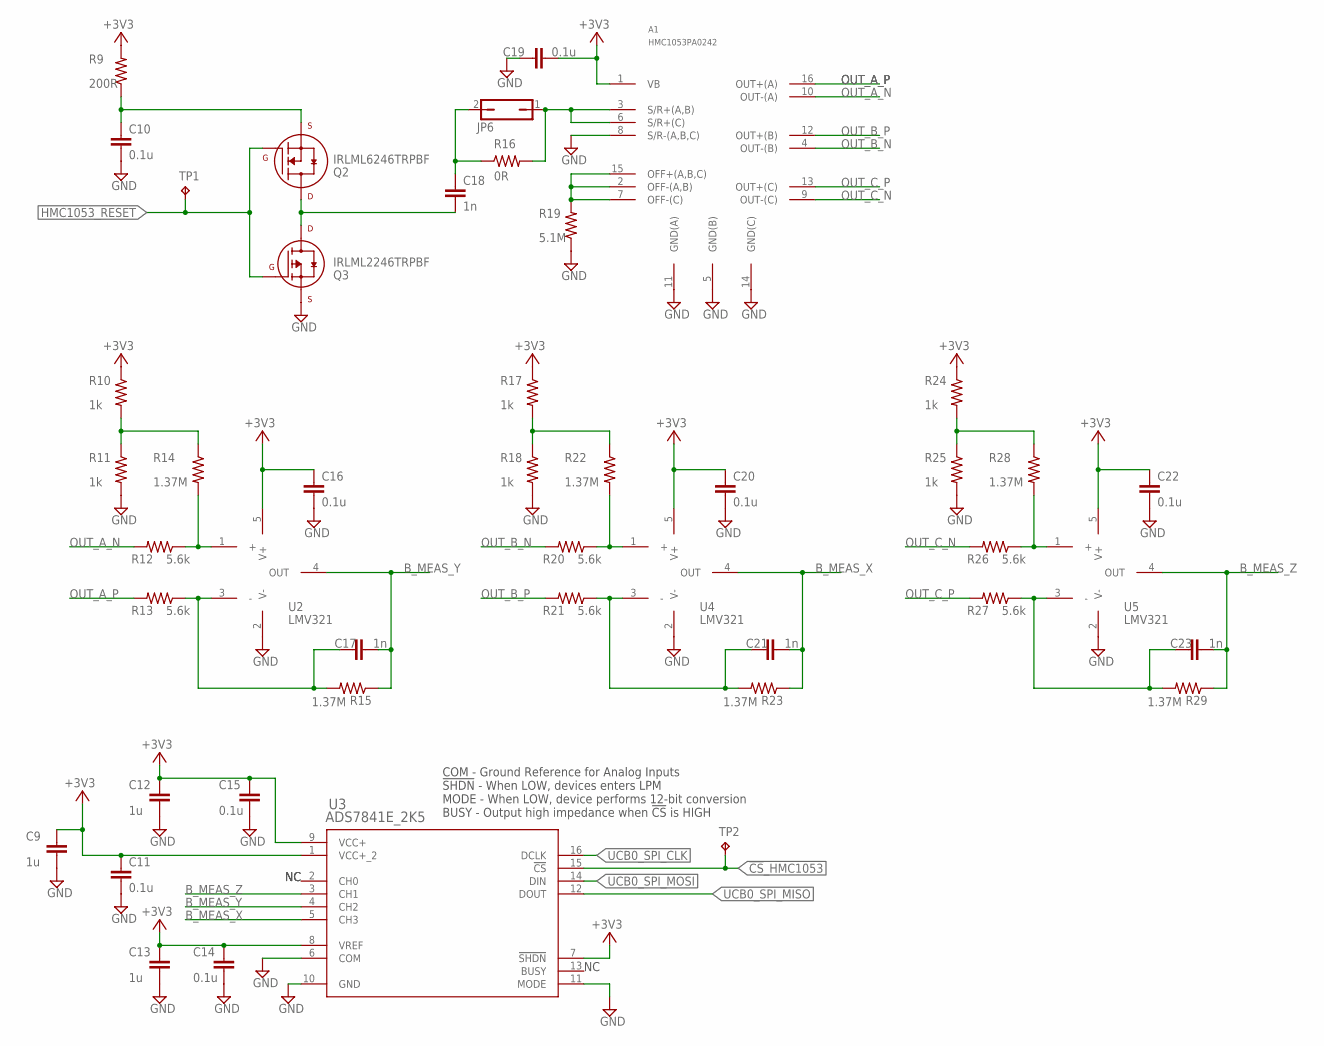
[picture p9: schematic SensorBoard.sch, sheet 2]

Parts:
A1: HMC1053PA0242; PA0242
C9, C12, C13: 1u; C0805
C10, C11, C14, C15, C16, C19, C20, C22: 0.1u; C0603
C17, C21, C23: 1n; C0805
C18: 1n; C1206
JP6: JP1Q_; 1X02
Q2: IRLML6246TRPBF; SOT23-3P95_237X112L25X40N_MICRO3
Q3: IRLML2246TRPBF; SOT23-3P95_237X112L25X40N_MICRO3
R9: 200R; R0805
R10, R11, R17, R18, R24, R25: 1k; R0805
R12, R13, R20, R21, R26, R27: 5.6k; R0805
R14, R15, R22, R23, R28, R29: 1.37M; R0805
R16: 0R; R0805
R19: 5.1M; R0805
TP1, TP2: TESTPOINT; TP_P76H50
U2, U4, U5: LMV321; SC70-5P65_210X110L36X22N
U3: ADS7841E_2K5; DBQ16

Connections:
!CS!_HMC1053: TP2.1, U3.15 (!CS); also elsewhere on the board
+3V3: A1.1 (VB), C9.1, C11.1, C12.1, C13.1, C14.1, C15.1, C16.1, C19.1, C20.1, C22.1, R9.2, R10.1, R17.1, R24.1, U2.5 (V+), U3.1 (VCC+_2), U3.7 (!SHDN), U3.8 (VREF), U3.9 (VCC+), U4.5 (V+), U5.5 (V+); also elsewhere on the board
B_MEAS_X: C21.2, R23.1, U3.5 (CH3), U4.4 (OUT)
B_MEAS_Y: C17.2, R15.1, U2.4 (OUT), U3.4 (CH2)
B_MEAS_Z: C23.2, R29.1, U3.3 (CH1), U5.4 (OUT)
GND: A1.5 (GND(B)), A1.8 (S/R-(A,B,C)), A1.11 (GND(A)), A1.14 (GND(C)), C9.2, C10.1, C11.2, C12.2, C13.2, C14.2, C15.2, C16.2, C19.2, C20.2, C22.2, Q3.2 (S), R11.2, R18.2, R19.1, R25.2, U2.2 (V-), U3.6 (COM), U3.10 (GND), U3.11 (MODE), U4.2 (V-), U5.2 (V-); also elsewhere on the board
HMC1053_RESET: Q2.1 (G), Q3.1 (G), TP1.1; also elsewhere on the board
unnamed: C18.1, Q2.3 (D), Q3.3 (D)
unnamed: R10.2, R11.1, R14.1
unnamed: C17.1, R13.1, R15.2, U2.3 (-)
unnamed: R12.1, R14.2, U2.1 (+)
unnamed: C18.2, JP6.2, R16.1
unnamed: A1.2 (OFF-(A,B)), A1.7 (OFF-(C)), A1.15 (OFF+(A,B,C)), R19.2
unnamed: A1.3 (S/R+(A,B)), A1.6 (S/R+(C)), JP6.1, R16.2
unnamed: C10.2, Q2.2 (S), R9.1
unnamed: R17.2, R18.1, R22.1
unnamed: C21.1, R21.1, R23.2, U4.3 (-)
unnamed: R20.1, R22.2, U4.1 (+)
unnamed: R24.2, R25.1, R28.1
unnamed: C23.1, R27.1, R29.2, U5.3 (-)
unnamed: R26.1, R28.2, U5.1 (+)
OUT_A_N: A1.10 (OUT-(A)), R12.2
OUT_A_P: A1.16 (OUT+(A)), R13.2
OUT_B_N: A1.4 (OUT-(B)), R20.2
OUT_B_P: A1.12 (OUT+(B)), R21.2
OUT_C_N: A1.9 (OUT-(C)), R26.2
OUT_C_P: A1.13 (OUT+(C)), R27.2
UCB0_SPI_CLK: U3.16 (DCLK); also elsewhere on the board
UCB0_SPI_MISO: U3.12 (DOUT); also elsewhere on the board
UCB0_SPI_MOSI: U3.14 (DIN); also elsewhere on the board

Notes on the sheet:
COM - Ground Reference for Analog Inputs !SHDN! - When LOW, devices enters LPM MODE - When LOW, device performs 12-bit conversion BUSY - Output high impedance when !CS! is HIGH

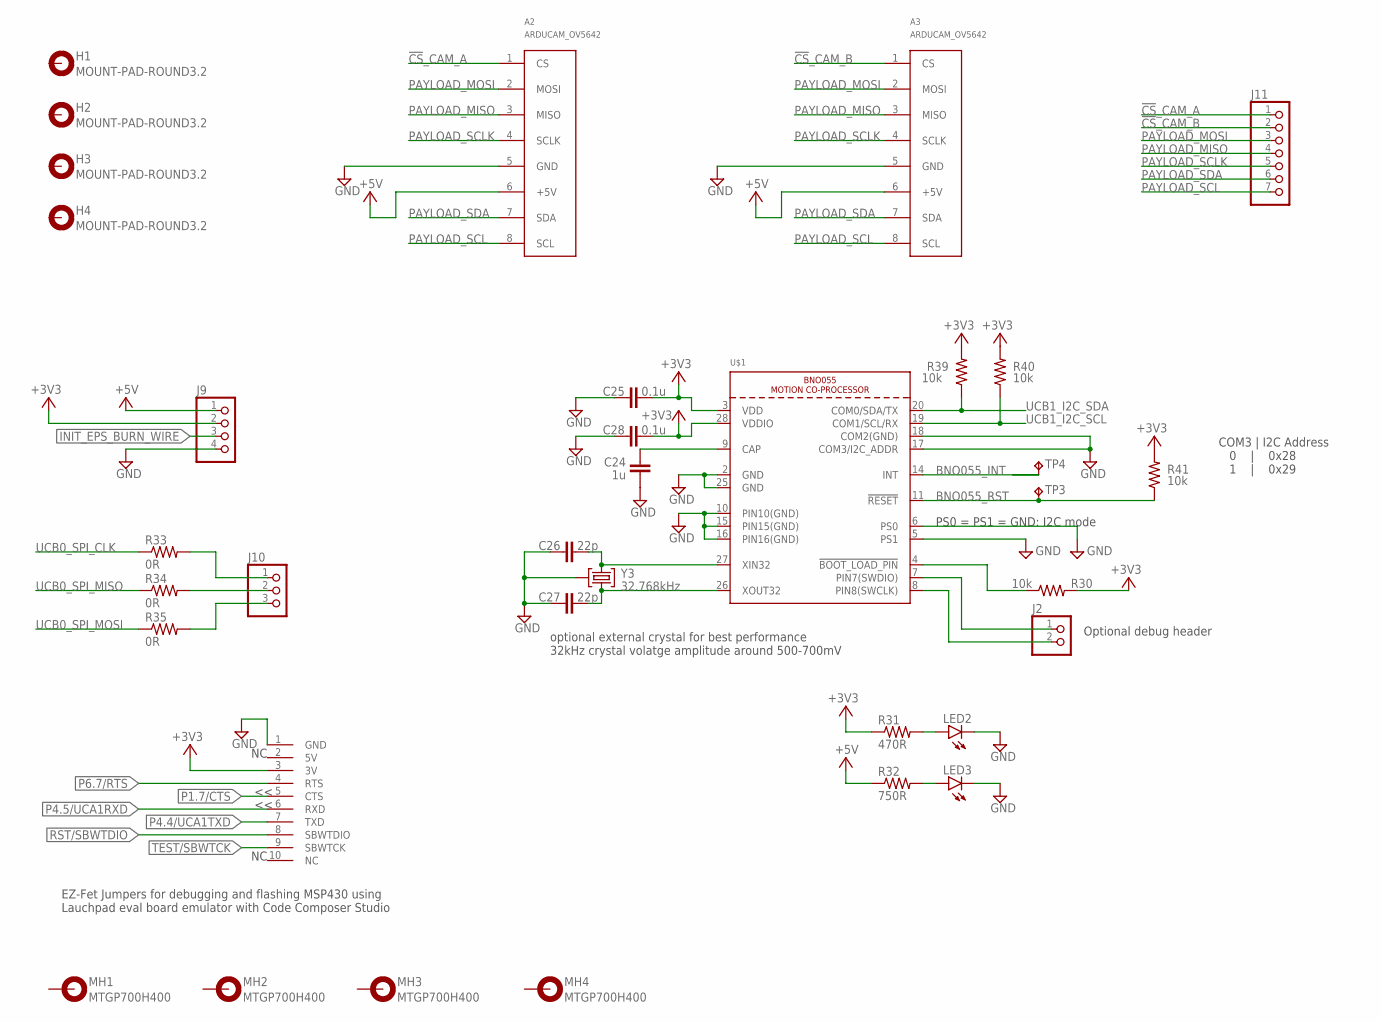
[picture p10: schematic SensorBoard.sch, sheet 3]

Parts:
A2, A3: ARDUCAM_OV5642; ARDUCAM
C24: 1u; C0402
C25, C28: 0.1u; C0402
C26, C27: 22p; C0402
H1, H2, H3, H4: MOUNT-PAD-ROUND3.2; 3,2-PAD
J1: HDR_10_EZFET_DEBUGGER; HDRV10W66P254_10X1_2540X254H858
J2: HDR_1X2_; 1X02
J9: PINHD-1X4; 1X04
J10: PINHD-1X3; 1X03
J11: PINHD-1X7; 1X07
LED2, LED3: LEDCHIP-LED0603; CHIP-LED0603
MH1, MH2, MH3, MH4: MTGP700H400
R30, R39, R40, R41: 10k; R0402
R31: 470R; R0603
R32: 750R; R0603
R33, R34, R35: 0R; R0805
TP3, TP4: TESTPOINT; TP_P76H50
U$1: BNO055
Y3: 32.768kHz; MS3V-T1R

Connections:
!CS!_CAM_A: A2.1 (CS), J11.1
!CS!_CAM_B: A3.1 (CS), J11.2
+3V3: C25.2, C28.2, J1.3 (3V), J9.2, R30.2, R31.1, R39.2, R40.2, R41.2, U$1.3 (VDD), U$1.28 (VDDIO); also elsewhere on the board
+5V: A2.6 (+5V), A3.6 (+5V), J9.1, R32.1; also elsewhere on the board
BNO055_INT: TP4.1, U$1.14 (INT)
BNO055_RST: R41.1, TP3.1, U$1.11 (!RESET)
GND: A2.5 (GND), A3.5 (GND), C24.1, C25.1, C26.1, C27.1, C28.1, J1.1 (GND), J9.4, LED2.C, LED3.C, U$1.2 (GND), U$1.5 (PS1), U$1.6 (PS0), U$1.10 (PIN10(GND)), U$1.15 (PIN15(GND)), U$1.16 (PIN16(GND)), U$1.17 (COM3/I2C_ADDR), U$1.18 (COM2(GND)), U$1.25 (GND), Y3.P3 (GND); also elsewhere on the board
INIT_EPS_BURN_WIRE: J9.3; also elsewhere on the board
unnamed: J10.1, R33.2
unnamed: J10.2, R34.2
unnamed: J10.3, R35.2
unnamed: LED2.A, R31.2
unnamed: LED3.A, R32.2
unnamed: R30.1, U$1.4 (!BOOT_LOAD_PIN)
unnamed: C24.2, U$1.9 (CAP)
unnamed: C26.2, U$1.27 (XIN32), Y3.P2 (2)
unnamed: C27.2, U$1.26 (XOUT32), Y3.P1 (1)
unnamed: J2.1, U$1.7 (PIN7(SWDIO))
unnamed: J2.2, U$1.8 (PIN8(SWCLK))
P1.7/CTS: J1.5 (CTS); also elsewhere on the board
P4.4/UCA1TXD: J1.7 (TXD); also elsewhere on the board
P4.5/UCA1RXD: J1.6 (RXD); also elsewhere on the board
P6.7/RTS: J1.4 (RTS); also elsewhere on the board
PAYLOAD_MISO: A2.3 (MISO), A3.3 (MISO), J11.4
PAYLOAD_MOSI: A2.2 (MOSI), A3.2 (MOSI), J11.3
PAYLOAD_SCL: A2.8 (SCL), A3.8 (SCL), J11.7
PAYLOAD_SCLK: A2.4 (SCLK), A3.4 (SCLK), J11.5
PAYLOAD_SDA: A2.7 (SDA), A3.7 (SDA), J11.6
RST/SBWTDIO: J1.8 (SBWTDIO); also elsewhere on the board
TEST/SBWTCK: J1.9 (SBWTCK); also elsewhere on the board
UCB0_SPI_CLK: R33.1; also elsewhere on the board
UCB0_SPI_MISO: R34.1; also elsewhere on the board
UCB0_SPI_MOSI: R35.1; also elsewhere on the board
UCB1_I2C_SCL: R40.1, U$1.19 (COM1/SCL/RX); also elsewhere on the board
UCB1_I2C_SDA: R39.1, U$1.20 (COM0/SDA/TX); also elsewhere on the board

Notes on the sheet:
EZ-Fet Jumpers for debugging and flashing MSP430 using Lauchpad eval board emulator with Code Composer Studio
optional external crystal for best performance 32kHz crystal volatge amplitude around 500-700mV
Optional debug header
PS0 = PS1 = GND: I2C mode
COM3 | I2C Address 0 | 0x28 1 | 0x29

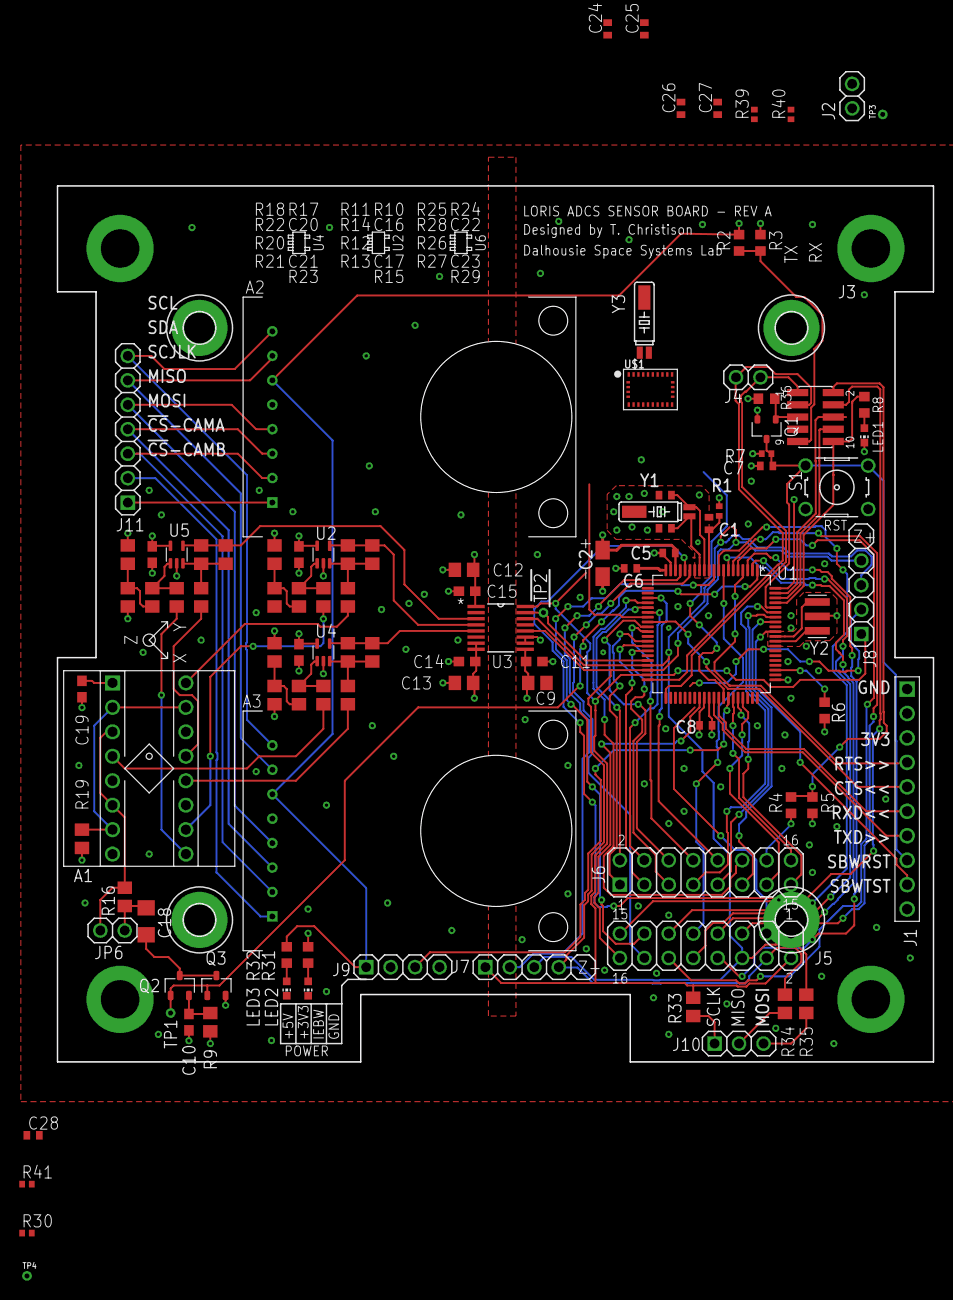
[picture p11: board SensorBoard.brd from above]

Board: 4 copper layers, 91.0 x 91.0 mm, 110 parts (0 on the bottom side), 105 nets.

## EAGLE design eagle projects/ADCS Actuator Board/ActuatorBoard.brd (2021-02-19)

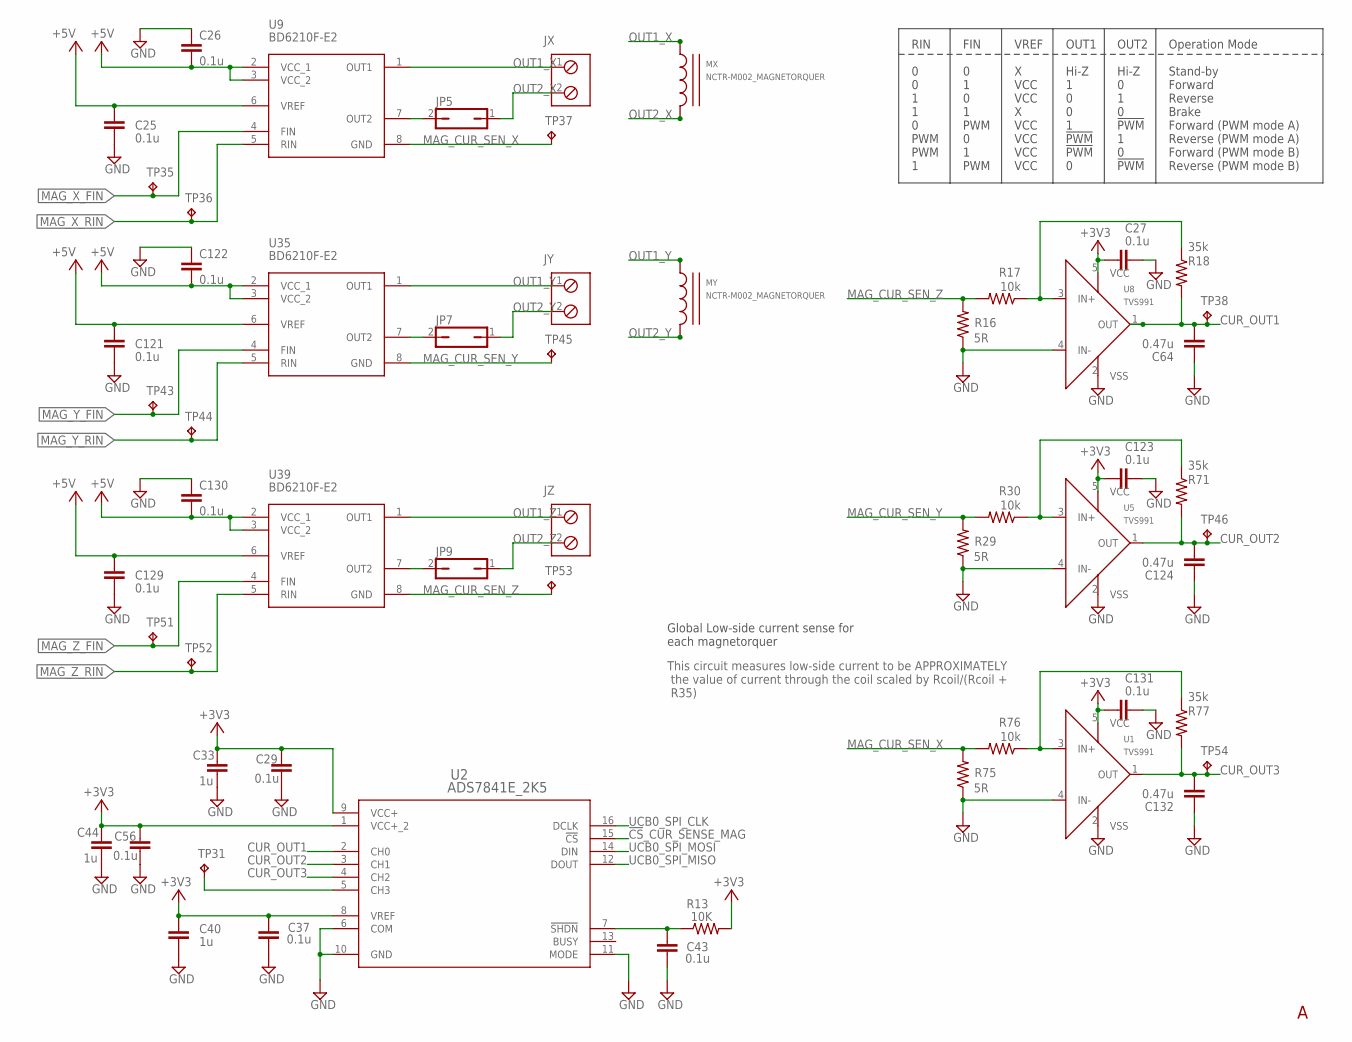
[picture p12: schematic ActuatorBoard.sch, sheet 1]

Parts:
C25, C26, C121, C122, C129, C130: 0.1u; C0603
C27, C29, C37, C43, C56, C123, C131: 0.1u; C0402
C33, C40, C44: 1u; C0402
C64, C124, C132: 0.47u; C0603
JP5, JP7, JP9: JP1Q_; 1X02
JX: TRM_BLK_1X2; 2POL254
JY: TRM_BLK_1X2; 2POL254
JZ: TRM_BLK_1X2; 2POL254
MX: NCTR-M002_MAGNETORQUER; MAG_MOUNT_V3
MY: NCTR-M002_MAGNETORQUER; MAG_MOUNT_V3
R13: 10K; R0402
R16, R29, R75: 5R; R0402
R17, R30, R76: 10k; R0402
R18, R71, R77: 35k; R0402
TP31, TP35, TP36, TP37, TP38, TP43, TP44, TP45, TP46, TP51, TP52, TP53, TP54: TESTPOINT; TP_P76H50
U1, U5, U8: TVS991; SOT95P280X145-5N
U2: ADS7841E_2K5; DBQ16
U9, U35, U39: BD6210F-E2; BD6221F-E2_SOIC8P127_500X620X171L30X42N

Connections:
!CS!_CUR_SENSE_MAG: U2.15 (!CS); also elsewhere on the board
+3V3: C27.1, C29.1, C33.1, C37.1, C40.1, C44.1, C56.1, C123.1, C131.1, R13.2, U1.5 (VCC), U2.1 (VCC+_2), U2.8 (VREF), U2.9 (VCC+), U5.5 (VCC), U8.5 (VCC); also elsewhere on the board
+5V: C25.1, C26.2, C121.1, C122.2, C129.1, C130.2, U9.2 (VCC_1), U9.3 (VCC_2), U9.6 (VREF), U35.2 (VCC_1), U35.3 (VCC_2), U35.6 (VREF), U39.2 (VCC_1), U39.3 (VCC_2), U39.6 (VREF); also elsewhere on the board
CUR_OUT1: C64.2, R18.2, TP38.1, U2.2 (CH0), U8.1 (OUT)
CUR_OUT2: C124.2, R71.2, TP46.1, U2.3 (CH1), U5.1 (OUT)
CUR_OUT3: C132.2, R77.2, TP54.1, U1.1 (OUT), U2.4 (CH2)
GND: C25.2, C26.1, C27.2, C29.2, C33.2, C37.2, C40.2, C43.2, C44.2, C56.2, C64.1, C121.2, C122.1, C123.2, C124.1, C129.2, C130.1, C131.2, C132.1, R16.1, R29.1, R75.1, U1.2 (VSS), U1.4 (IN-), U2.6 (COM), U2.10 (GND), U2.11 (MODE), U5.2 (VSS), U5.4 (IN-), U8.2 (VSS), U8.4 (IN-); also elsewhere on the board
MAG_CUR_SEN_X: R75.2, R76.2, TP37.1, U9.8 (GND)
MAG_CUR_SEN_Y: R29.2, R30.2, TP45.1, U35.8 (GND)
MAG_CUR_SEN_Z: R16.2, R17.2, TP53.1, U39.8 (GND)
MAG_X_FIN: TP35.1, U9.4 (FIN); also elsewhere on the board
MAG_X_RIN: TP36.1, U9.5 (RIN); also elsewhere on the board
MAG_Y_FIN: TP43.1, U35.4 (FIN); also elsewhere on the board
MAG_Y_RIN: TP44.1, U35.5 (RIN); also elsewhere on the board
MAG_Z_FIN: TP51.1, U39.4 (FIN); also elsewhere on the board
MAG_Z_RIN: TP52.1, U39.5 (RIN); also elsewhere on the board
unnamed: C43.1, R13.1, U2.7 (!SHDN)
unnamed: TP31.1, U2.5 (CH3)
unnamed: JP5.2, U9.7 (OUT2)
unnamed: R17.1, R18.1, U8.3 (IN+)
unnamed: JP7.2, U35.7 (OUT2)
unnamed: R30.1, R71.1, U5.3 (IN+)
unnamed: JP9.2, U39.7 (OUT2)
unnamed: R76.1, R77.1, U1.3 (IN+)
OUT1_X: JX.1, U9.1 (OUT1)
OUT1_Y: JY.1, U35.1 (OUT1)
OUT1_Z: JZ.1, U39.1 (OUT1)
OUT2_X: JP5.1, JX.2
OUT2_Y: JP7.1, JY.2
OUT2_Z: JP9.1, JZ.2
UCB0_SPI_CLK: U2.16 (DCLK); also elsewhere on the board
UCB0_SPI_MISO: U2.12 (DOUT); also elsewhere on the board
UCB0_SPI_MOSI: U2.14 (DIN); also elsewhere on the board

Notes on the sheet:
FIN 0 1 0 1 PWM 0 1 PWM
RIN 0 0 1 1 0 PWM PWM 1
VREF X VCC VCC X VCC VCC VCC VCC
OUT1 Hi-Z 1 0 0 1 !PWM !PWM 0
OUT2 Hi-Z 0 1 0 !PWM 1 0 !PWM
Operation Mode Stand-by Forward Reverse Brake Forward (PWM mode A) Reverse (PWM mode A) Forward (PWM mode B) Reverse (PWM mode B)
Global Low-side current sense for each magnetorquer
This circuit measures low-side current to be APPROXIMATELY the value of current through the coil scaled by Rcoil/(Rcoil + R35)

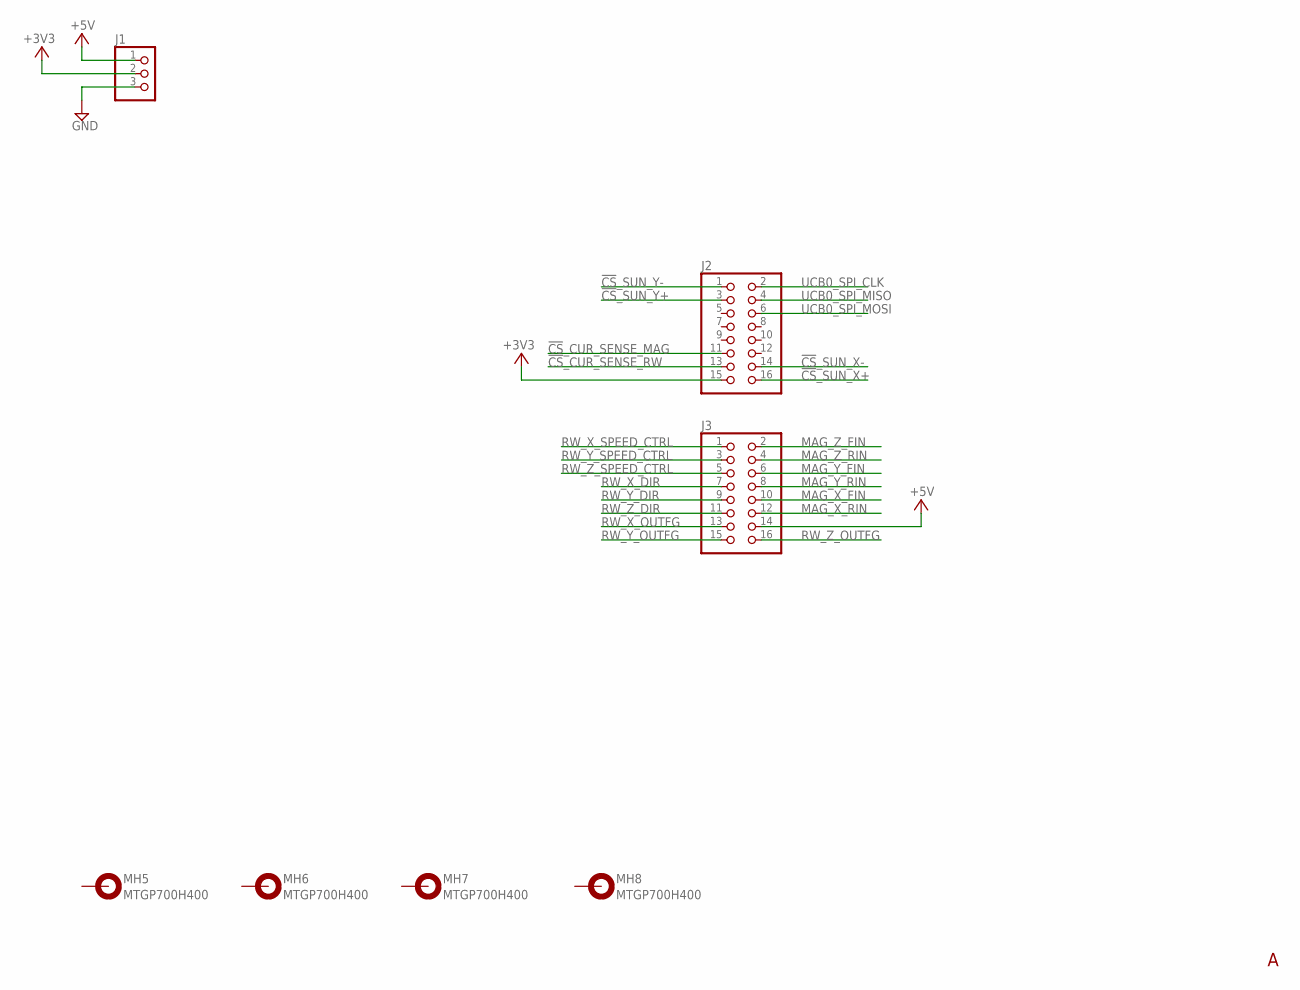
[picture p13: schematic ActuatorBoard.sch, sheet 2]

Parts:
J1: PINHD-1X3; 1X03
J2, J3: PINHD-2X8_TXT-MOVED; 2X08_TXT-MOVED
MH5, MH6, MH7, MH8: MTGP700H400

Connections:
!CS!_CUR_SENSE_MAG: J2.11; also elsewhere on the board
!CS!_CUR_SENSE_RW: J2.13; also elsewhere on the board
!CS!_SUN_X+: J2.16; also elsewhere on the board
!CS!_SUN_X-: J2.14; also elsewhere on the board
!CS!_SUN_Y+: J2.3; also elsewhere on the board
!CS!_SUN_Y-: J2.1; also elsewhere on the board
+3V3: J1.2, J2.15; also elsewhere on the board
+5V: J1.1, J3.14; also elsewhere on the board
GND: J1.3; also elsewhere on the board
MAG_X_FIN: J3.10; also elsewhere on the board
MAG_X_RIN: J3.12; also elsewhere on the board
MAG_Y_FIN: J3.6; also elsewhere on the board
MAG_Y_RIN: J3.8; also elsewhere on the board
MAG_Z_FIN: J3.2; also elsewhere on the board
MAG_Z_RIN: J3.4; also elsewhere on the board
RW_X_DIR: J3.7; also elsewhere on the board
RW_X_OUTFG: J3.13; also elsewhere on the board
RW_X_SPEED_CTRL: J3.1; also elsewhere on the board
RW_Y_DIR: J3.9; also elsewhere on the board
RW_Y_OUTFG: J3.15; also elsewhere on the board
RW_Y_SPEED_CTRL: J3.3; also elsewhere on the board
RW_Z_DIR: J3.11; also elsewhere on the board
RW_Z_OUTFG: J3.16; also elsewhere on the board
RW_Z_SPEED_CTRL: J3.5; also elsewhere on the board
UCB0_SPI_CLK: J2.2; also elsewhere on the board
UCB0_SPI_MISO: J2.4; also elsewhere on the board
UCB0_SPI_MOSI: J2.6; also elsewhere on the board

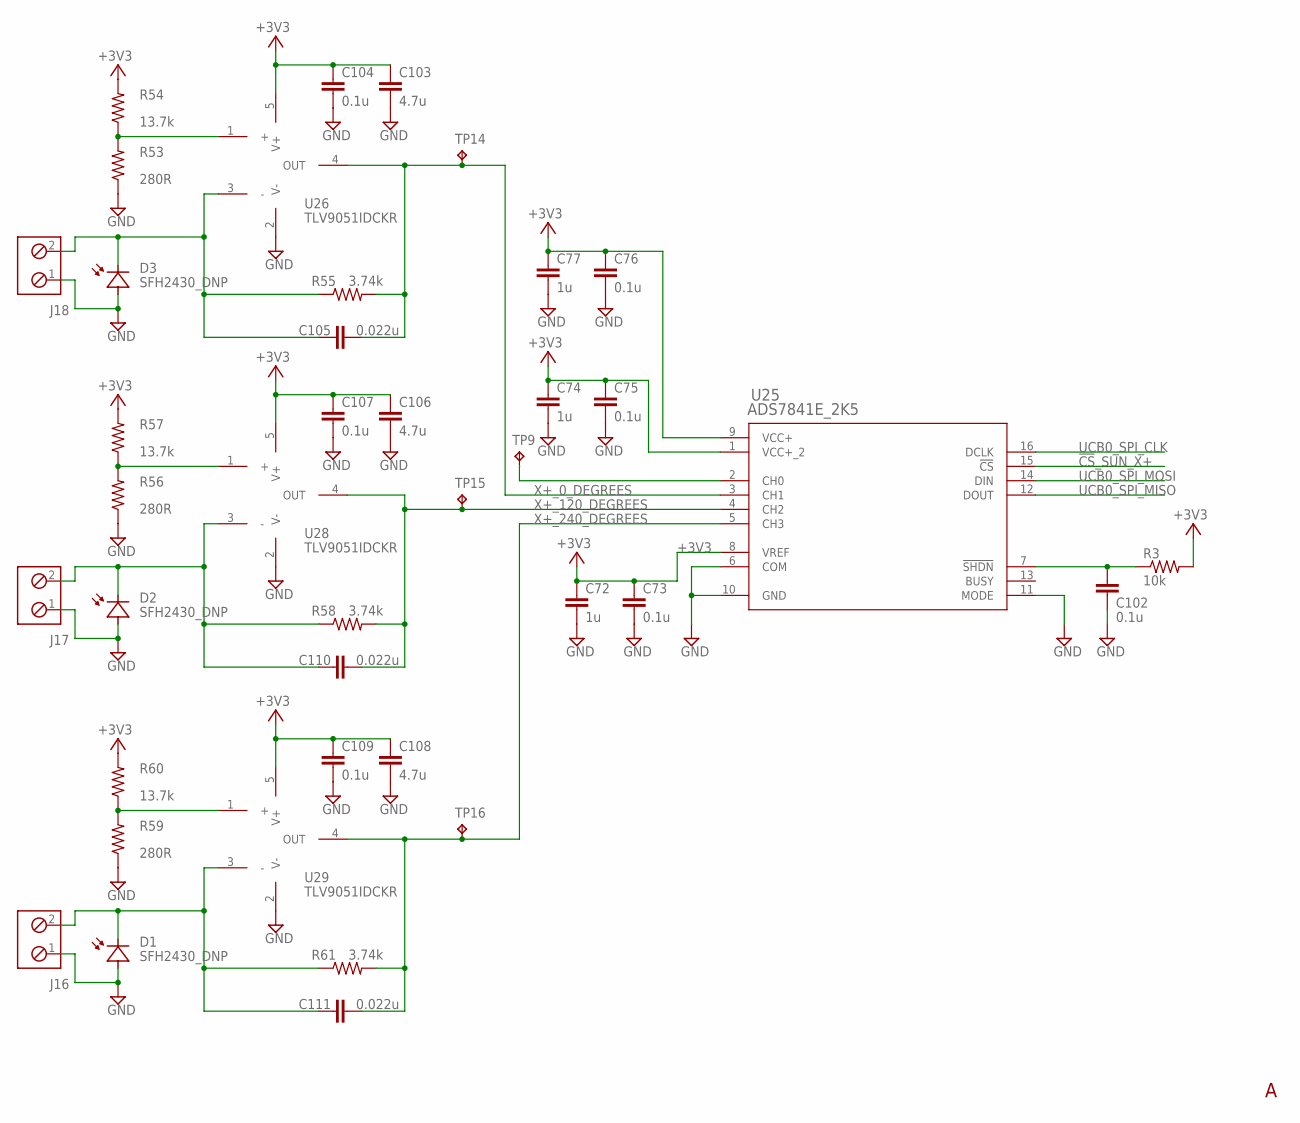
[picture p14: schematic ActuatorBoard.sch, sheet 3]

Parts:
C72, C74, C77: 1u; C0402
C73, C75, C76, C102, C104, C107, C109: 0.1u; C0402
C103, C106, C108: 4.7u; C0402
C105, C110, C111: 0.022u; C0402
J16, J17, J18: TRM_BLK_1X2; 2POL254
R3: 10k; R0402
R53, R56, R59: 280R; R0402
R54, R57, R60: 13.7k; R0402
R55, R58, R61: 3.74k; R0402
TP9, TP14, TP15, TP16: TESTPOINT; TP_P76H50
U25: ADS7841E_2K5; DBQ16
U26, U28, U29: TLV9051IDCKR; SC70-5P65_210X110L36X22N_TLV9051

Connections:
!CS!_SUN_X+: U25.15 (!CS); also elsewhere on the board
+3V3: C72.1, C73.1, C74.1, C75.1, C76.1, C77.1, C103.1, C104.1, C106.1, C107.1, C108.1, C109.1, R3.2, R54.2, R57.2, R60.2, U25.1 (VCC+_2), U25.8 (VREF), U25.9 (VCC+), U26.5 (V+), U28.5 (V+), U29.5 (V+); also elsewhere on the board
GND: C72.2, C73.2, C74.2, C75.2, C76.2, C77.2, C102.2, C103.2, C104.2, C106.2, C107.2, C108.2, C109.2, J16.1, J17.1, J18.1, R53.1, R56.1, R59.1, U25.6 (COM), U25.10 (GND), U25.11 (MODE), U26.2 (V-), U28.2 (V-), U29.2 (V-); also elsewhere on the board
unnamed: TP9.1, U25.2 (CH0)
unnamed: C102.1, R3.1, U25.7 (!SHDN)
unnamed: C105.1, J18.2, R55.1, U26.3 (-)
unnamed: R53.2, R54.1, U26.1 (+)
unnamed: C110.1, J17.2, R58.1, U28.3 (-)
unnamed: R56.2, R57.1, U28.1 (+)
unnamed: C111.1, J16.2, R61.1, U29.3 (-)
unnamed: R59.2, R60.1, U29.1 (+)
UCB0_SPI_CLK: U25.16 (DCLK); also elsewhere on the board
UCB0_SPI_MISO: U25.12 (DOUT); also elsewhere on the board
UCB0_SPI_MOSI: U25.14 (DIN); also elsewhere on the board
X+_0_DEGREES: C105.2, R55.2, TP14.1, U25.3 (CH1), U26.4 (OUT)
X+_120_DEGREES: C110.2, R58.2, TP15.1, U25.4 (CH2), U28.4 (OUT)
X+_240_DEGREES: C111.2, R61.2, TP16.1, U25.5 (CH3), U29.4 (OUT)

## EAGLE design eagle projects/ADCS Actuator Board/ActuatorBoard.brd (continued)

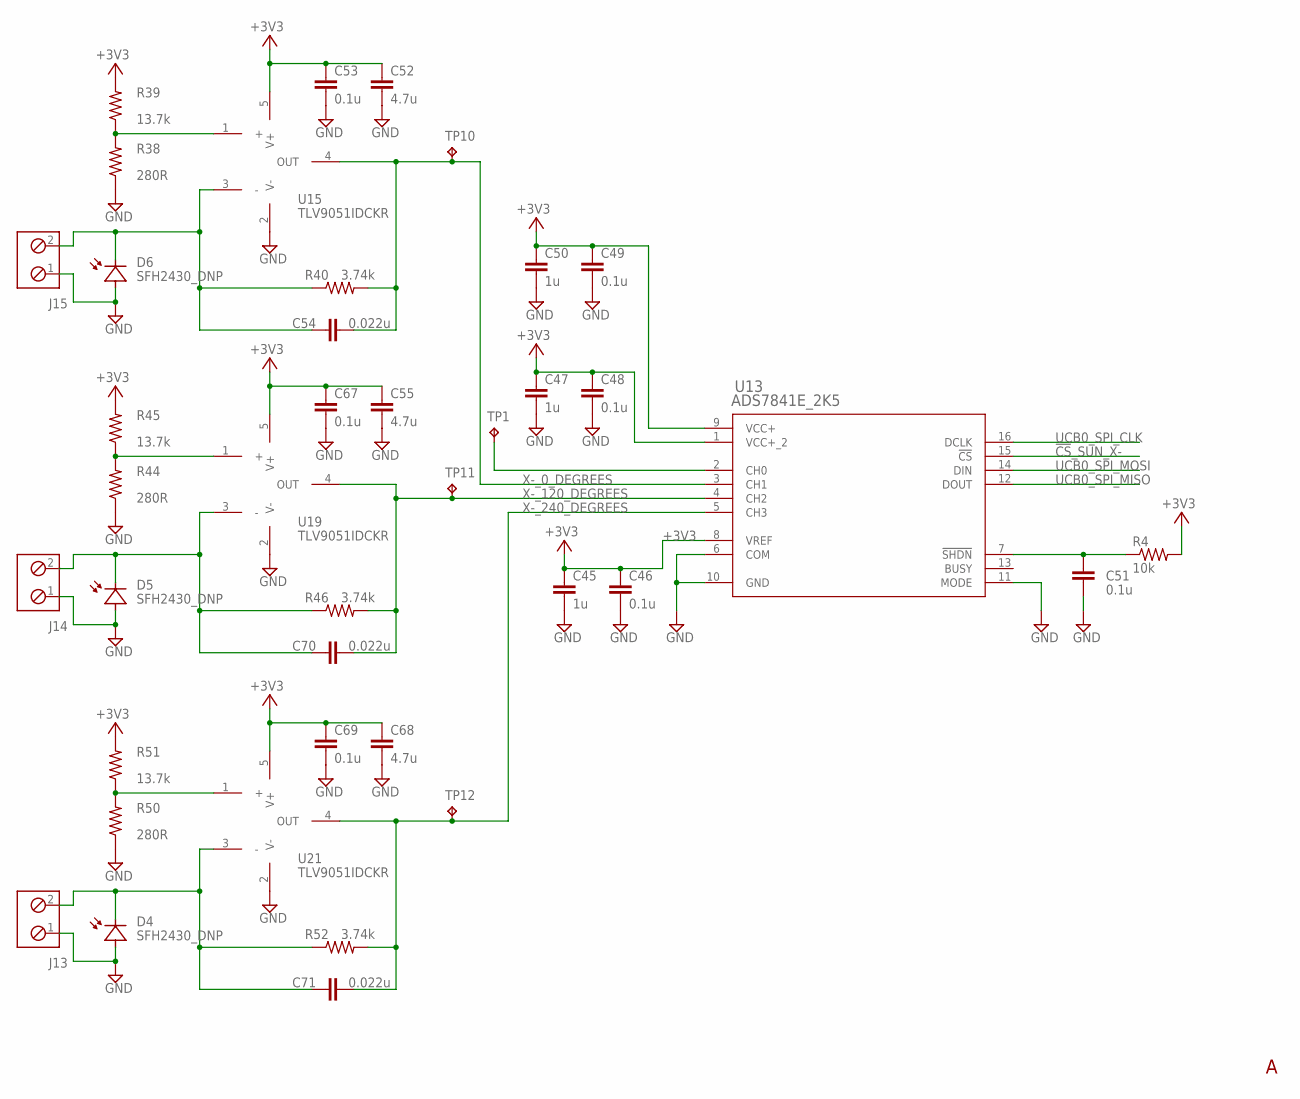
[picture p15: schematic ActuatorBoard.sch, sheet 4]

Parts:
C45, C47, C50: 1u; C0402
C46, C48, C49, C51, C53, C67, C69: 0.1u; C0402
C52, C55, C68: 4.7u; C0402
C54, C70, C71: 0.022u; C0402
J13, J14, J15: TRM_BLK_1X2; 2POL254
R4: 10k; R0402
R38, R44, R50: 280R; R0402
R39, R45, R51: 13.7k; R0402
R40, R46, R52: 3.74k; R0402
TP1, TP10, TP11, TP12: TESTPOINT; TP_P76H50
U13: ADS7841E_2K5; DBQ16
U15, U19, U21: TLV9051IDCKR; SC70-5P65_210X110L36X22N_TLV9051

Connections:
!CS!_SUN_X-: U13.15 (!CS); also elsewhere on the board
+3V3: C45.1, C46.1, C47.1, C48.1, C49.1, C50.1, C52.1, C53.1, C55.1, C67.1, C68.1, C69.1, R4.2, R39.2, R45.2, R51.2, U13.1 (VCC+_2), U13.8 (VREF), U13.9 (VCC+), U15.5 (V+), U19.5 (V+), U21.5 (V+); also elsewhere on the board
GND: C45.2, C46.2, C47.2, C48.2, C49.2, C50.2, C51.2, C52.2, C53.2, C55.2, C67.2, C68.2, C69.2, J13.1, J14.1, J15.1, R38.1, R44.1, R50.1, U13.6 (COM), U13.10 (GND), U13.11 (MODE), U15.2 (V-), U19.2 (V-), U21.2 (V-); also elsewhere on the board
unnamed: TP1.1, U13.2 (CH0)
unnamed: C51.1, R4.1, U13.7 (!SHDN)
unnamed: C54.1, J15.2, R40.1, U15.3 (-)
unnamed: R38.2, R39.1, U15.1 (+)
unnamed: C70.1, J14.2, R46.1, U19.3 (-)
unnamed: R44.2, R45.1, U19.1 (+)
unnamed: C71.1, J13.2, R52.1, U21.3 (-)
unnamed: R50.2, R51.1, U21.1 (+)
UCB0_SPI_CLK: U13.16 (DCLK); also elsewhere on the board
UCB0_SPI_MISO: U13.12 (DOUT); also elsewhere on the board
UCB0_SPI_MOSI: U13.14 (DIN); also elsewhere on the board
X-_0_DEGREES: C54.2, R40.2, TP10.1, U13.3 (CH1), U15.4 (OUT)
X-_120_DEGREES: C70.2, R46.2, TP11.1, U13.4 (CH2), U19.4 (OUT)
X-_240_DEGREES: C71.2, R52.2, TP12.1, U13.5 (CH3), U21.4 (OUT)

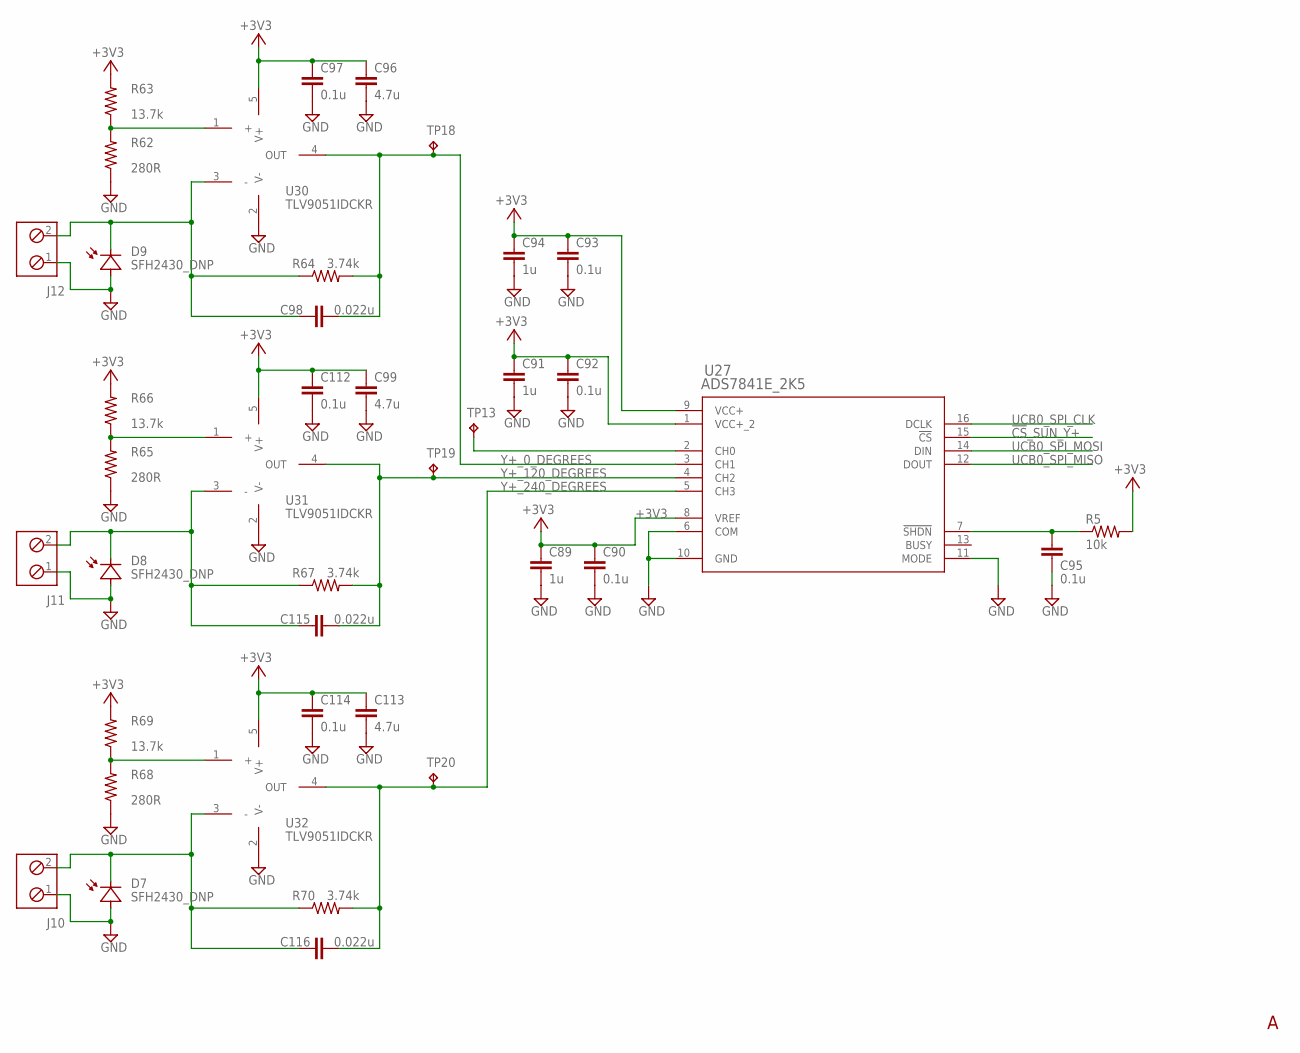
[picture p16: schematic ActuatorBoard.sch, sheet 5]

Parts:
C89, C91, C94: 1u; C0402
C90, C92, C93, C95, C97, C112, C114: 0.1u; C0402
C96, C99, C113: 4.7u; C0402
C98, C115, C116: 0.022u; C0402
J10, J11, J12: TRM_BLK_1X2; 2POL254
R5: 10k; R0402
R62, R65, R68: 280R; R0402
R63, R66, R69: 13.7k; R0402
R64, R67, R70: 3.74k; R0402
TP13, TP18, TP19, TP20: TESTPOINT; TP_P76H50
U27: ADS7841E_2K5; DBQ16
U30, U31, U32: TLV9051IDCKR; SC70-5P65_210X110L36X22N_TLV9051

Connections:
!CS!_SUN_Y+: U27.15 (!CS); also elsewhere on the board
+3V3: C89.1, C90.1, C91.1, C92.1, C93.1, C94.1, C96.1, C97.1, C99.1, C112.1, C113.1, C114.1, R5.2, R63.2, R66.2, R69.2, U27.1 (VCC+_2), U27.8 (VREF), U27.9 (VCC+), U30.5 (V+), U31.5 (V+), U32.5 (V+); also elsewhere on the board
GND: C89.2, C90.2, C91.2, C92.2, C93.2, C94.2, C95.2, C96.2, C97.2, C99.2, C112.2, C113.2, C114.2, J10.1, J11.1, J12.1, R62.1, R65.1, R68.1, U27.6 (COM), U27.10 (GND), U27.11 (MODE), U30.2 (V-), U31.2 (V-), U32.2 (V-); also elsewhere on the board
unnamed: TP13.1, U27.2 (CH0)
unnamed: C95.1, R5.1, U27.7 (!SHDN)
unnamed: C98.1, J12.2, R64.1, U30.3 (-)
unnamed: R62.2, R63.1, U30.1 (+)
unnamed: C115.1, J11.2, R67.1, U31.3 (-)
unnamed: R65.2, R66.1, U31.1 (+)
unnamed: C116.1, J10.2, R70.1, U32.3 (-)
unnamed: R68.2, R69.1, U32.1 (+)
UCB0_SPI_CLK: U27.16 (DCLK); also elsewhere on the board
UCB0_SPI_MISO: U27.12 (DOUT); also elsewhere on the board
UCB0_SPI_MOSI: U27.14 (DIN); also elsewhere on the board
Y+_0_DEGREES: C98.2, R64.2, TP18.1, U27.3 (CH1), U30.4 (OUT)
Y+_120_DEGREES: C115.2, R67.2, TP19.1, U27.4 (CH2), U31.4 (OUT)
Y+_240_DEGREES: C116.2, R70.2, TP20.1, U27.5 (CH3), U32.4 (OUT)

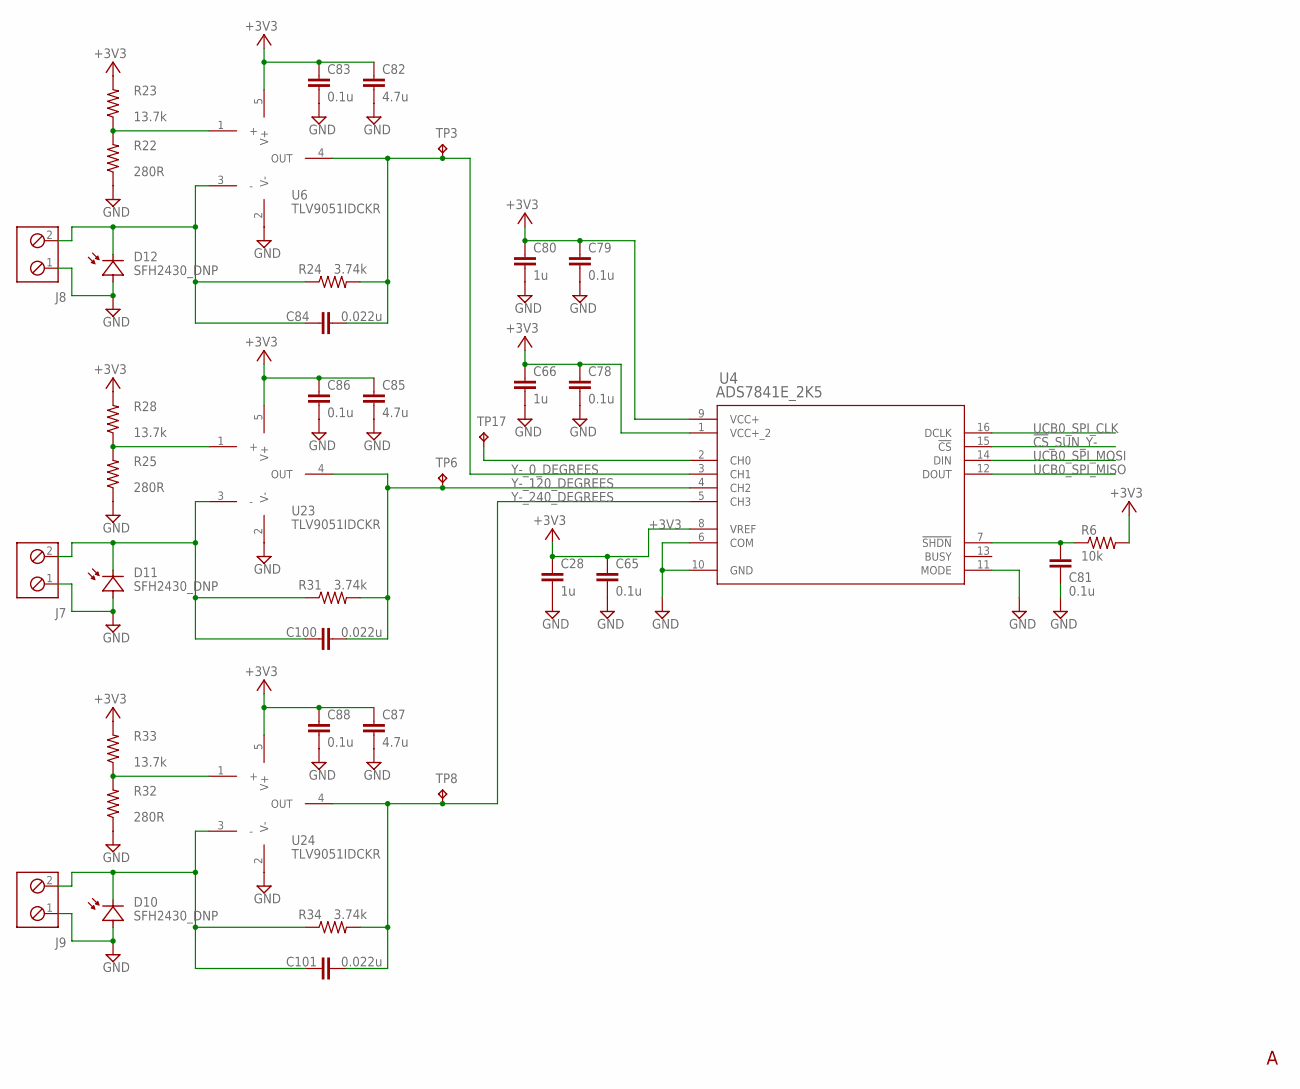
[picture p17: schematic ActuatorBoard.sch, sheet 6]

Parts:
C28, C66, C80: 1u; C0402
C65, C78, C79, C81, C83, C86, C88: 0.1u; C0402
C82, C85, C87: 4.7u; C0402
C84, C100, C101: 0.022u; C0402
J7, J8, J9: TRM_BLK_1X2; 2POL254
R6: 10k; R0402
R22, R25, R32: 280R; R0402
R23, R28, R33: 13.7k; R0402
R24, R31, R34: 3.74k; R0402
TP3, TP6, TP8, TP17: TESTPOINT; TP_P76H50
U4: ADS7841E_2K5; DBQ16
U6, U23, U24: TLV9051IDCKR; SC70-5P65_210X110L36X22N_TLV9051

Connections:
!CS!_SUN_Y-: U4.15 (!CS); also elsewhere on the board
+3V3: C28.1, C65.1, C66.1, C78.1, C79.1, C80.1, C82.1, C83.1, C85.1, C86.1, C87.1, C88.1, R6.2, R23.2, R28.2, R33.2, U4.1 (VCC+_2), U4.8 (VREF), U4.9 (VCC+), U6.5 (V+), U23.5 (V+), U24.5 (V+); also elsewhere on the board
GND: C28.2, C65.2, C66.2, C78.2, C79.2, C80.2, C81.2, C82.2, C83.2, C85.2, C86.2, C87.2, C88.2, J7.1, J8.1, J9.1, R22.1, R25.1, R32.1, U4.6 (COM), U4.10 (GND), U4.11 (MODE), U6.2 (V-), U23.2 (V-), U24.2 (V-); also elsewhere on the board
unnamed: TP17.1, U4.2 (CH0)
unnamed: C100.1, J7.2, R31.1, U23.3 (-)
unnamed: C81.1, R6.1, U4.7 (!SHDN)
unnamed: C84.1, J8.2, R24.1, U6.3 (-)
unnamed: R22.2, R23.1, U6.1 (+)
unnamed: R25.2, R28.1, U23.1 (+)
unnamed: C101.1, J9.2, R34.1, U24.3 (-)
unnamed: R32.2, R33.1, U24.1 (+)
UCB0_SPI_CLK: U4.16 (DCLK); also elsewhere on the board
UCB0_SPI_MISO: U4.12 (DOUT); also elsewhere on the board
UCB0_SPI_MOSI: U4.14 (DIN); also elsewhere on the board
Y-_0_DEGREES: C84.2, R24.2, TP3.1, U4.3 (CH1), U6.4 (OUT)
Y-_120_DEGREES: C100.2, R31.2, TP6.1, U4.4 (CH2), U23.4 (OUT)
Y-_240_DEGREES: C101.2, R34.2, TP8.1, U4.5 (CH3), U24.4 (OUT)

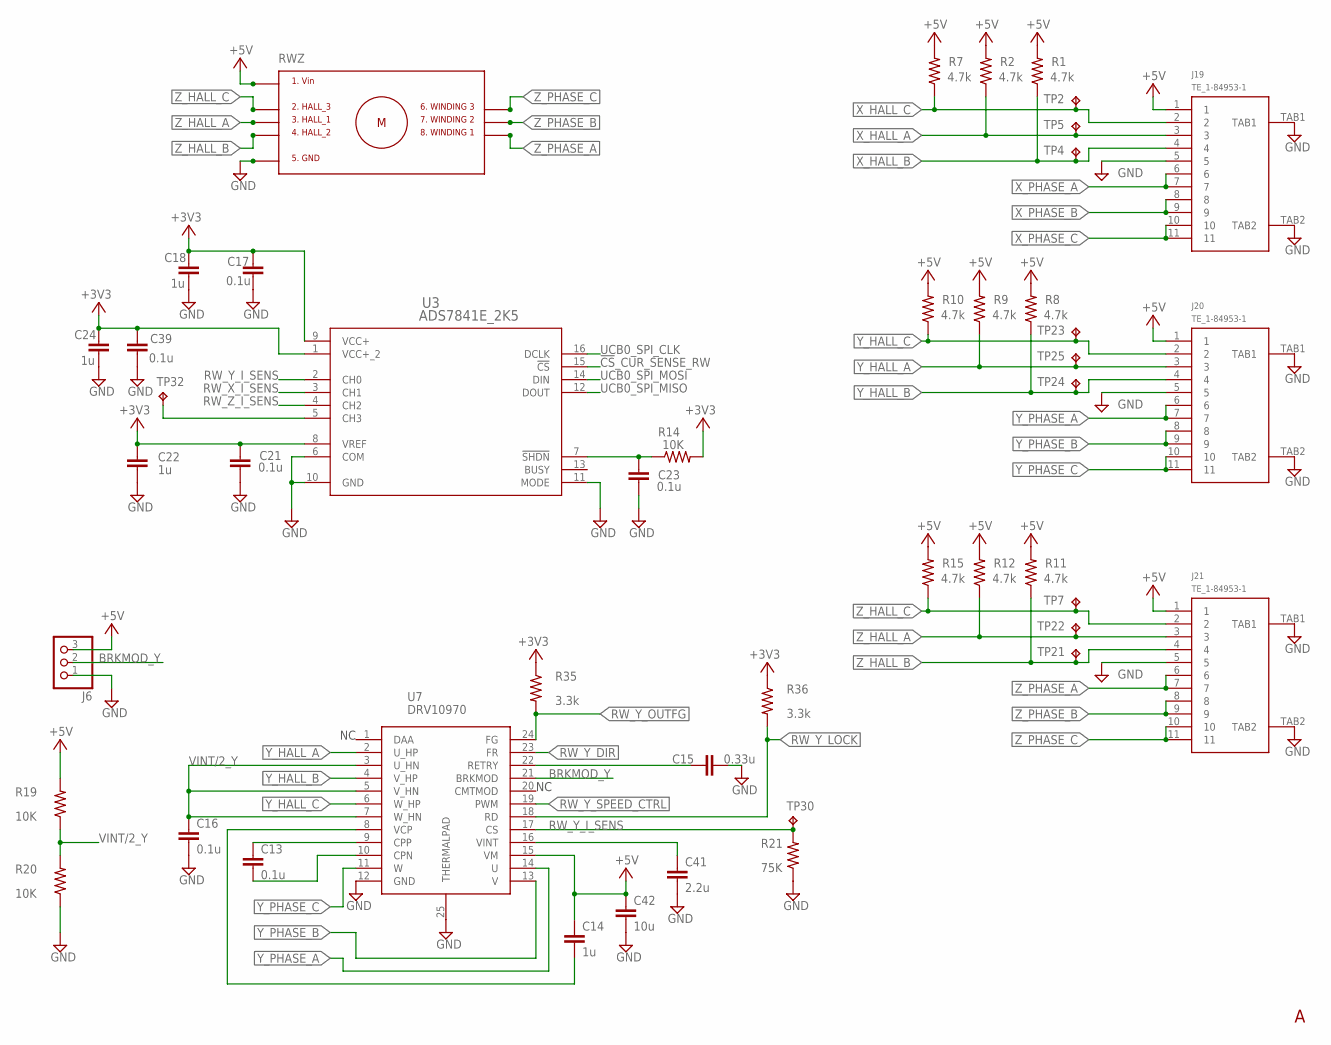
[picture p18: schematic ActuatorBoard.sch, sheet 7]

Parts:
C13, C16: 0.1u; C0603
C14: 1u; C0603
C15: 0.33u; C0603
C17, C21, C23, C39: 0.1u; C0402
C18, C22, C24: 1u; C0402
C41: 2.2u; C0603
C42: 10u; C0603
J6: PINHD-1X3; 1X03
J19, J20, J21: TE_1-84953-1
R1, R2, R7, R8, R9, R10, R11, R12, R15: 4.7k; R0402
R14: 10K; R0402
R19, R20: 10K; R0603
R21: 75K; R0603
R35, R36: 3.3k; R0603
RWZ: REACTION_WHEEL_NOPINS_MAXON; RWA_NOPINS
TP2, TP4, TP5, TP7, TP21, TP22, TP23, TP24, TP25, TP30, TP32: TESTPOINT; TP_P76H50
U3: ADS7841E_2K5; DBQ16
U7: DRV10970_MOTOR_DRIVERDRV10970; SOP65P640X120-25T240X328N

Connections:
!CS!_CUR_SENSE_RW: U3.15 (!CS); also elsewhere on the board
+3V3: C17.1, C18.1, C21.1, C22.1, C24.1, C39.1, R14.2, R35.1, R36.1, U3.1 (VCC+_2), U3.8 (VREF), U3.9 (VCC+); also elsewhere on the board
+5V: C14.1, C42.1, J6.3, J19.1, J20.1, J21.1, R1.2, R2.2, R7.2, R8.2, R9.2, R10.2, R11.2, R12.2, R15.2, R19.2, U7.15 (VM); also elsewhere on the board
BRKMOD_Y: J6.2, U7.21 (BRKMOD)
GND: C15.2, C16.2, C17.2, C18.2, C21.2, C22.2, C23.2, C24.2, C39.2, C41.2, C42.2, J6.1, J19.5, J19.TAB1, J19.TAB2, J20.5, J20.TAB1, J20.TAB2, J21.5, J21.TAB1, J21.TAB2, R20.1, R21.1, U3.6 (COM), U3.10 (GND), U3.11 (MODE), U7.12 (GND), U7.25 (THERMALPAD); also elsewhere on the board
unnamed: C23.1, R14.1, U3.7 (!SHDN)
unnamed: TP32.1, U3.5 (CH3)
unnamed: C13.1, U7.9 (CPP)
unnamed: C14.2, U7.8 (VCP)
unnamed: C13.2, U7.10 (CPN)
unnamed: C41.1, U7.16 (VINT)
unnamed: C15.1, U7.22 (RETRY)
RW_X_I_SENS: U3.3 (CH1); also elsewhere on the board
RW_Y_DIR: U7.23 (FR); also elsewhere on the board
RW_Y_I_SENS: R21.2, TP30.1, U3.2 (CH0), U7.17 (CS)
RW_Y_LOCK: R36.2, U7.18 (RD)
RW_Y_OUTFG: R35.2, U7.24 (FG); also elsewhere on the board
RW_Y_SPEED_CTRL: U7.19 (PWM); also elsewhere on the board
RW_Z_I_SENS: U3.4 (CH2); also elsewhere on the board
UCB0_SPI_CLK: U3.16 (DCLK); also elsewhere on the board
UCB0_SPI_MISO: U3.12 (DOUT); also elsewhere on the board
UCB0_SPI_MOSI: U3.14 (DIN); also elsewhere on the board
VINT/2_Y: C16.1, R19.1, R20.2, U7.3 (U_HN), U7.5 (V_HN), U7.7 (W_HN)
X_HALL_A: J19.3, R2.1, TP5.1; also elsewhere on the board
X_HALL_B: J19.4, R1.1, TP4.1; also elsewhere on the board
X_HALL_C: J19.2, R7.1, TP2.1; also elsewhere on the board
X_PHASE_A: J19.6, J19.7; also elsewhere on the board
X_PHASE_B: J19.8, J19.9; also elsewhere on the board
X_PHASE_C: J19.10, J19.11; also elsewhere on the board
Y_HALL_A: J20.3, R9.1, TP25.1, U7.2 (U_HP)
Y_HALL_B: J20.4, R8.1, TP24.1, U7.4 (V_HP)
Y_HALL_C: J20.2, R10.1, TP23.1, U7.6 (W_HP)
Y_PHASE_A: J20.6, J20.7, U7.14 (U)
Y_PHASE_B: J20.8, J20.9, U7.13 (V)
Y_PHASE_C: J20.10, J20.11, U7.11 (W)
Z_HALL_A: J21.3, R12.1, TP22.1; also elsewhere on the board
Z_HALL_B: J21.4, R11.1, TP21.1; also elsewhere on the board
Z_HALL_C: J21.2, R15.1, TP7.1; also elsewhere on the board
Z_PHASE_A: J21.6, J21.7; also elsewhere on the board
Z_PHASE_B: J21.8, J21.9; also elsewhere on the board
Z_PHASE_C: J21.10, J21.11; also elsewhere on the board


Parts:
C119, C126, C139, C142: 0.1u; C0603
C120, C140: 1u; C0603
C125, C141: 0.33u; C0603
C127, C143: 2.2u; C0603
C128, C144: 10u; C0603
J4, J5: PINHD-1X3; 1X03
LED1, LED2: LEDCHIPLED_0603; CHIPLED_0603
R26, R27: 500R; R0603
R48, R49, R83, R84: 10K; R0603
R72, R85: 75K; R0603
R73, R74, R86, R87: 3.3k; R0603
TP34, TP40: TESTPOINT; TP_P76H50
U10, U12: DRV10970_MOTOR_DRIVERDRV10970; SOP65P640X120-25T240X328N

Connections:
+3V3: LED2.A, R73.1, R74.1, R86.1, R87.1; also elsewhere on the board
+5V: C120.1, C128.1, C140.1, C144.1, J4.3, J5.3, LED1.A, R48.2, R83.2, U10.15 (VM), U12.15 (VM); also elsewhere on the board
BRKMOD_X: J4.2, U10.21 (BRKMOD)
BRKMOD_Z: J5.2, U12.21 (BRKMOD)
GND: C125.2, C126.2, C127.2, C128.2, C141.2, C142.2, C143.2, C144.2, J4.1, J5.1, R26.1, R27.1, R49.1, R72.1, R84.1, R85.1, U10.12 (GND), U10.25 (THERMALPAD), U12.12 (GND), U12.25 (THERMALPAD); also elsewhere on the board
unnamed: LED1.C, R26.2
unnamed: LED2.C, R27.2
unnamed: C119.1, U10.9 (CPP)
unnamed: C120.2, U10.8 (VCP)
unnamed: C119.2, U10.10 (CPN)
unnamed: C127.1, U10.16 (VINT)
unnamed: C125.1, U10.22 (RETRY)
unnamed: C139.1, U12.9 (CPP)
unnamed: C140.2, U12.8 (VCP)
unnamed: C139.2, U12.10 (CPN)
unnamed: C143.1, U12.16 (VINT)
unnamed: C141.1, U12.22 (RETRY)
RW_X_DIR: U10.23 (FR); also elsewhere on the board
RW_X_I_SENS: R72.2, TP34.1, U10.17 (CS); also elsewhere on the board
RW_X_LOCK: R74.2, U10.18 (RD)
RW_X_OUTFG: R73.2, U10.24 (FG); also elsewhere on the board
RW_X_SPEED_CTRL: U10.19 (PWM); also elsewhere on the board
RW_Z_DIR: U12.23 (FR); also elsewhere on the board
RW_Z_I_SENS: R85.2, TP40.1, U12.17 (CS); also elsewhere on the board
RW_Z_LOCK: R87.2, U12.18 (RD)
RW_Z_OUTFG: R86.2, U12.24 (FG); also elsewhere on the board
RW_Z_SPEED_CTRL: U12.19 (PWM); also elsewhere on the board
VINT/2_X: C126.1, R48.1, R49.2, U10.3 (U_HN), U10.5 (V_HN), U10.7 (W_HN)
VINT/2_Z: C142.1, R83.1, R84.2, U12.3 (U_HN), U12.5 (V_HN), U12.7 (W_HN)
X_HALL_A: U10.2 (U_HP); also elsewhere on the board
X_HALL_B: U10.4 (V_HP); also elsewhere on the board
X_HALL_C: U10.6 (W_HP); also elsewhere on the board
X_PHASE_A: U10.14 (U); also elsewhere on the board
X_PHASE_B: U10.13 (V); also elsewhere on the board
X_PHASE_C: U10.11 (W); also elsewhere on the board
Z_HALL_A: U12.2 (U_HP); also elsewhere on the board
Z_HALL_B: U12.4 (V_HP); also elsewhere on the board
Z_HALL_C: U12.6 (W_HP); also elsewhere on the board
Z_PHASE_A: U12.14 (U); also elsewhere on the board
Z_PHASE_B: U12.13 (V); also elsewhere on the board
Z_PHASE_C: U12.11 (W); also elsewhere on the board

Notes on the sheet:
CPN CPP: Connect 0.1u X7R cap between between CPN and CPP VM: Power Supply, decouple with 10u cap VINT: Bypass with 2.2u cap rated for 10V VCP: Connect a 16V 1-uF cap to VM CS: Connect a resistor to adhjust the current limit
DAA: Drive angle adjustment configuration pin - Low: 10 degree angle adjustment - High: 5 degree angle adhustment - Floating: Adaptive angle adjustment BRKMOD: Brake mode setting - low = phases tri-state - high = phases driven low RETRY: Auto retry timing configurable with cap (see datasheet Eq2 fo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
CMTMOD: Commutation mode setting - Low: Sinusoidal operation mode with 0° Hall placement - High: Sinusoidal operation mode with 30° Hall placement - Floating: Trapezoidal operation mode with 30° Hall placement Trapezoidal control selected. Requires hall sensors unlike sinusoidal



Board: 4 copper layers, 91.0 x 91.0 mm, 290 parts (238 on the bottom side), 140 nets.

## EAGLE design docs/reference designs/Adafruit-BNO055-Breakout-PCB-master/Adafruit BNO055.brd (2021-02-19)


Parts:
C1, C2: 22pF; 0805-NO
C3: 0.1uF; 0805-NO
C4: 0.1uF; 0805_10MGAP
C5: 10uF; 0805-NO
C6: 10uF; 0805_10MGAP
D1: 1n4148; SOD-323
FID1, FID2: FIDUCIAL""; FIDUCIAL_1MM
JP1: HEADER-1X676MIL; 1X06_ROUND_76
JP2: HEADER-1X476MIL; 1X04_ROUND_76
Q1, Q2: BSS138; SOT23-WIDE
R3, R4, R5, R6, R7, R10: 10K; 0805-NO
R8, R9: 10K; _0805MP
U1: MIC5225-3.3; SOT23-5
U$2: BNO055
U$29, U$30, U$31, U$32: MOUNTINGHOLE2.5_THICK; MOUNTINGHOLE_2.5_PLATED_THICK
Y1: 32.768kHz; CRYSTAL_8X3.8

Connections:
3.3V: C4.2, C6.1, JP1.2, Q1.1 (G), Q2.1 (G), R6.2, R7.2, R10.2, U1.5 (OUT), U$2.3 (VDD), U$2.4 (NBOOT_LOAD_PIN), U$2.28 (VDDIO)
5.0V: C5.1, JP1.1, R8.2, R9.2, U1.1 (IN), U1.3 (EN)
GND: C1.1, C2.1, C3.1, C4.1, C5.2, C6.2, JP1.3, R3.2, R4.2, R5.2, U1.2 (GND), U$2.2 (GND), U$2.10 (PIN10(GND)), U$2.15 (PIN15(GND)), U$2.16 (PIN16(GND)), U$2.18 (COM2(GND)), U$2.25 (GND)
I2CADDR_3V: JP2.4, R5.1, U$2.17 (COM3/I2C_ADDR)
INT_3V: JP2.3, U$2.14 (INT)
unnamed: C1.2, U$2.27 (XIN32), Y1.P$4 (2)
unnamed: C2.2, U$2.26 (XOUT32), Y1.P$1 (1)
unnamed: C3.2, U$2.9 (CAP)
NRESET_3V: D1.A, R10.1, U$2.11 (NRESET)
PS0_3V: JP2.1, R3.1, U$2.6 (PS0)
PS1_3V: JP2.2, R4.1, U$2.5 (PS1)
RST_5V: D1.C, JP1.6
SCL_3V: Q2.2 (S), R7.1, U$2.19 (COM1/SCL/RX)
SCL_5V: JP1.5, Q2.3 (D), R9.1
SDA_3V: Q1.2 (S), R6.1, U$2.20 (COM0/SDA/TX)
SDA_5V: JP1.4, Q1.3 (D), R8.1



Board: 2 copper layers, 26.7 x 20.3 mm, 31 parts (2 on the bottom side), 16 nets.

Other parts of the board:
U$3: PCBFEAT-REV-040
U$28: ADAFRUIT_TEXT_20MM
U$33: ADAFRUIT_2.5MM

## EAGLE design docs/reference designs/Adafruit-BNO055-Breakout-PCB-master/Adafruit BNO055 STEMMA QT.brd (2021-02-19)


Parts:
C1, C2: 22pF; 0603-NO
C3, C9: 0.1uF; 0603-NO
C7, C8: 10uF; 0805-NO
CONN3, CONN4: STEMMA_I2C_QT; JST_SH4
D1: 1n4148; SOD-323
D2: GREEN; CHIPLED_0603_NOOUTLINE
FID3, FID4: FIDUCIAL_1MM
JP2: HEADER-1X476MIL; 1X04_ROUND_76
JP3: HEADER-1X670MIL; 1X06_ROUND_70
Q3: BSS138; SOT363
R1, R3: 10K; RESPACK_4X0603
R4: 10K; 0603-NO
SJ1: SOLDERJUMPER; SOLDERJUMPER_ARROW_NOPASTE
U2: AP2112K-3.3; SOT23-5
U$2: BNO055
U$45, U$46, U$48, U$49: MOUNTINGHOLE2.5; MOUNTINGHOLE_2.5_PLATED
X2: 32.768; XTAL3215

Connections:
3.3V: C8.1, C9.1, JP3.2, Q3.2 (G), Q3.5 (G), R1.1, R1.4 (1), R3.1, R4.1, SJ1.2, U2.5 (OUT), U$2.3 (VDD), U$2.4 (NBOOT_LOAD_PIN), U$2.8 (PIN8(SWCLK)), U$2.28 (VDDIO)
GND: C1.1, C2.1, C3.1, C7.2, C8.2, C9.2, CONN3.1 (GND), CONN3.MT1 (MT), CONN3.MT2 (MT), CONN4.1 (GND), CONN4.MT1 (MT), CONN4.MT2 (MT), D2.C, JP3.3, R3.2 (1), R3.5 (2), R3.6 (2), U2.2 (GND), U$2.2 (GND), U$2.10 (PIN10(GND)), U$2.15 (PIN15(GND)), U$2.16 (PIN16(GND)), U$2.18 (COM2(GND)), U$2.25 (GND)
I2CADDR_3V: JP2.2, R3.7 (2), SJ1.1, U$2.17 (COM3/I2C_ADDR)
INT_3V: JP2.1, U$2.14 (INT)
unnamed: C1.2, U$2.27 (XIN32), X2.P$2
unnamed: C2.2, U$2.26 (XOUT32), X2.P$1
unnamed: C3.2, U$2.9 (CAP)
unnamed: D2.A, R3.8 (2)
NRESET_3V: D1.A, R4.2, U$2.11 (NRESET)
PS0_3V: JP2.3, R3.3 (1), U$2.6 (PS0)
PS1_3V: JP2.4, R3.4 (1), U$2.5 (PS1)
RESET: D1.C, JP3.6
SCL: CONN3.4 (SCL), CONN4.4 (SCL), JP3.4, Q3.6 (D), R1.7 (2)
SCL_3V: Q3.1 (S), R1.5 (2), U$2.19 (COM1/SCL/RX)
SDA: CONN3.3 (SDA), CONN4.3 (SDA), JP3.5, Q3.3 (D), R1.6 (2)
SDA_3V: Q3.4 (S), R1.8 (2), U$2.20 (COM0/SDA/TX)
VCC: C7.1, CONN3.2 (V+), CONN4.2 (V+), JP3.1, R1.2 (1), R1.3 (1), U2.1 (IN), U2.3 (EN)

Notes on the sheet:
I2C Pullups & Shift
STEMMA/I2C Headers
ON LED
Power supply



Board: 2 copper layers, 25.4 x 20.3 mm, 30 parts (4 on the bottom side), 17 nets.

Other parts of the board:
U$51: ADAFRUIT_3.5MM
U$52: PCBFEAT-REV-040
U$53, U$54: STEMMAQT

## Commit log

2020-09-28 added project structure and readmes to the directories
    [bom.csv]
2020-10-05 Uploading eagle projects for actuator board and sensor board
    Also added eagle relevant information to main readme
    [01.brd, 01.sch, ActuatorBoard.brd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]
2020-10-05 Renamed sensor board files. Added notes to schematic for remaining work
    [SensorBoard.brd, SensorBoard.sch]
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2020-10-22 Board update commit before removing Z+ sunsensor from layout
    [SensorBoard.brd, SensorBoard.sch]
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2020-10-26 Updated placeholder footprints on actuator boards
    Added photodiode amplifier circuitry for X+/- and Y+/- faces
    [ActuatorBoard.brd, ActuatorBoard.sch]
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2020-10-28 Added speed counter circuitry (p3) and h-bridge logic table (p1)
    [ActuatorBoard.brd, ActuatorBoard.sch]
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2020-10-28 Added pinout and logic level shifting to speed counting circuitry
    [ActuatorBoard.brd, ActuatorBoard.sch]
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2020-10-30 Added cutouts to ground plane to separarte analog and digital
    [SensorBoard.brd]
2020-11-03 Added copper pours to top and bottom. Fixed silksreens, smoothed traces
    [SensorBoard.brd, SensorBoard.sch]
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2020-11-07 added indicator LEDs, drill legend, and adjusted board thickness
    [DRILEGEND.CFG, SensorBoard.brd, SensorBoard.sch]
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2020-11-07 Added testpoints, updated drill chart
    Added missing MTI-1 IMU reset signal to msp430
    [SensorBoard.brd, SensorBoard.sch]
2020-11-07 Fixed testpoint silkscreens, moved vias where silk interfered
    [SensorBoard.brd, SensorBoard.sch]
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2020-11-09 Replaced obsolete transistor Q2
    [SensorBoard.brd, SensorBoard.sch, Sensor_Board_BOM.xlsx]
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2020-11-19 Added releases. A.1 includes missing completed BOM
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2020-12-20 Updated logic level shifter mosfet packages and board dimensions
    [ZPlusSunSensorBoard.brd, ZPlusSunSensorBoard.sch]
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2020-12-21 Replaced logic level shift circuitry with simpler versions
    [ActuatorBoard.brd, ActuatorBoard.sch]
2020-12-22 updated schematic for proper wave cmp config and attached motors
    [ActuatorBoard.brd, ActuatorBoard.sch]
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2021-01-04 Updated board pinout to sensor board and pinout reformated first two pages for readability
    [ActuatorBoard.brd, ActuatorBoard.sch]
2021-01-04 made changes to motor driver and added new page with new motor drivers
    [ActuatorBoard.brd, ActuatorBoard.sch]
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2021-01-05 add initial implementation circuit of ADC for current sensing. Add shunt resistor value for current sensing comparator
    [ActuatorBoard.brd, ActuatorBoard.sch]
2021-01-06 Change shunt resistor value from 1R->5R on current sensing circuits for MQTR
    [ActuatorBoard.brd, ActuatorBoard.sch]
2021-01-08 removed old motor drivers and named current sens pins
    [ActuatorBoard.brd, ActuatorBoard.sch]
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2021-01-12 Update DR10970V motor driver IC footprint and symbol
    [ActuatorBoard.brd, ActuatorBoard.sch]
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2021-01-13 Add ground plane pour and change board stackup to 4 layers
    [ActuatorBoard.brd]
2021-01-13 Change silk font to vector style. Reduce size. Remove silkscreen component values to save space
    [ActuatorBoard.brd, ActuatorBoard.sch]
2021-01-13 Lock gnd plane in place and start work on power pour
    [ActuatorBoard.brd]
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2021-01-13 add DRC constraints from manufacturer, add initial layout routing for RW X and Y level shifters
    [ActuatorBoard.brd]
2021-01-14 Replaced photodiode circuitry with updated layout and values
    [ActuatorBoard.brd, ActuatorBoard.sch]
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2021-01-14 preliminary layout for reaction wheel circuitry and magnetorquers
    [ActuatorBoard.brd, ActuatorBoard.sch]
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2021-01-16 finished layout of all parts on board and most traces
    [ActuatorBoard.brd, ActuatorBoard.sch]
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2021-01-16 Resolve DRC clearance issues
    [ActuatorBoard.brd]
2021-01-17 Switched analog sensor circuitry to 3v3, added connectors for actuatrors (terminal blocks), and removed unneccessary actuator footprints, format adjustments
    [ActuatorBoard.brd, ActuatorBoard.sch]
2021-01-17 removed traces across the middle to clean up
    [ActuatorBoard.brd]
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2021-01-17 Found places for terminal blocks still need to look into the need for DMUX or not and switch rw x & y
    [ActuatorBoard.brd, ActuatorBoard.sch]
2021-01-17 swapped reaction wheel drivers X & Y
    [ActuatorBoard.brd, ActuatorBoard.sch]
2021-01-17 Replaced connector to match sensor board pinout
    [ActuatorBoard.brd, ActuatorBoard.sch]
2021-01-18 finished traces except for power and ground plane
    [ActuatorBoard.brd]
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2021-01-19 fixed net names for sun sensors
    [ActuatorBoard.brd, ActuatorBoard.sch]
2021-01-19 fixed design rule checks
    [ActuatorBoard.brd]
2021-01-19 replaced 10u caps with 4.7u
    [ActuatorBoard.brd, ActuatorBoard.sch]
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2021-01-20 I forgot to save changes to last commit
    [ActuatorBoard.brd]
2021-01-20 New sunsensor layout and updated sun sensor mask mount
    now all on 3v3 supply
    [ZPlusSunSensorBoard.brd, ZPlusSunSensorBoard.sch]
2021-01-21 Replaced Z- Sun sensor board with copy of Z+ sun sensor board
    [ZMinusSunSensorBoard.brd, ZMinusSunSensorBoard.sch]
2021-01-21 Added mounting holes for sun sensor board, added standoff mounting holes to sensor board
    [SensorBoard.brd, SensorBoard.sch, ZMinusSunSensorBoard.brd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]
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2021-01-28 Small value updates, new titleblock, and added bom
    [BOM_Z-SUNSENSE.xlsx, ZMinusSunSensorBoard.brd, ZMinusSunSensorBoard.sch]
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2021-01-29 Added boms for sun sense boards rev a
    [BOM_Z+SUNSENSE.xlsx, BOM_Z-SUNSENSE.xlsx]
2021-01-29 updates to Z+ sun sense board for 3d models
    [ZPlusSunSensorBoard.brd, ZPlusSunSensorBoard.sch]
2021-01-29 updates for 3d models for z- sun sense
    [ZMinusSunSensorBoard.brd, ZMinusSunSensorBoard.sch]
2021-01-29 fixed renamed h-bridge part in schematic/board
    [ActuatorBoard.brd]
2021-01-29 moved a bunch of digital shit around (work in progress). going to sleep now
    [ActuatorBoard.brd, ActuatorBoard.sch]
2021-01-29 finished rearranging analog side for minimal a/d ground bridge spacing
    [ActuatorBoard.brd, ActuatorBoard.sch]
2021-01-30 fixed silkscreen fiasco
    [ActuatorBoard.brd, ActuatorBoard.sch]
2021-02-01 Rerouted traces no drc errors except keepout around 1 TP
    [ActuatorBoard.brd]
2021-02-01 moved clk traces to be over ground plane
    [ActuatorBoard.brd]
2021-02-02 Added photodiode symbols without footprint and replaced title blocks
    [ActuatorBoard.sch]
2021-02-02 Fixed motordriver schematic for readability
    [ActuatorBoard.brd, ActuatorBoard.sch]
2021-02-02 Added missing decoupling caps and cleared ERC on schematic
    [ActuatorBoard.brd, ActuatorBoard.sch]
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2021-02-03 Moved h-bridges and current sensing around for magnetorquer control
    [ActuatorBoard.brd, ActuatorBoard.sch]
2021-02-03 Went ham. Changed motor driver layout.
    Bodied some beerz
    [ActuatorBoard.brd, ActuatorBoard.sch]
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2021-02-05 cleared drc errors ready for review
    [ActuatorBoard.brd]
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2021-02-12 Updated schematic fomatting and added DSS bitmap logo
    [ActuatorBoard.brd, ActuatorBoard.sch]
2021-02-12 fixed drc errors
    [ActuatorBoard.brd]
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2021-02-17 Replaced jumpers with circular pads
    [ActuatorBoard.brd, ActuatorBoard.sch]
2021-02-17 solved drc errors
    [ActuatorBoard.brd, ActuatorBoard.sch]
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2021-02-17 Replaced TVS991AILT opa,mp schematic symbol for readability
    [ActuatorBoard.brd, ActuatorBoard.sch]
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2021-02-17 I think i fixed it
    [ActuatorBoard.brd, ActuatorBoard.sch]
2021-02-17 Silk & via fix
    [ActuatorBoard.brd]
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

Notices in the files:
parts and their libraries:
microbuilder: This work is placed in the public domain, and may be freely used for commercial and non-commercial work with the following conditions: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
